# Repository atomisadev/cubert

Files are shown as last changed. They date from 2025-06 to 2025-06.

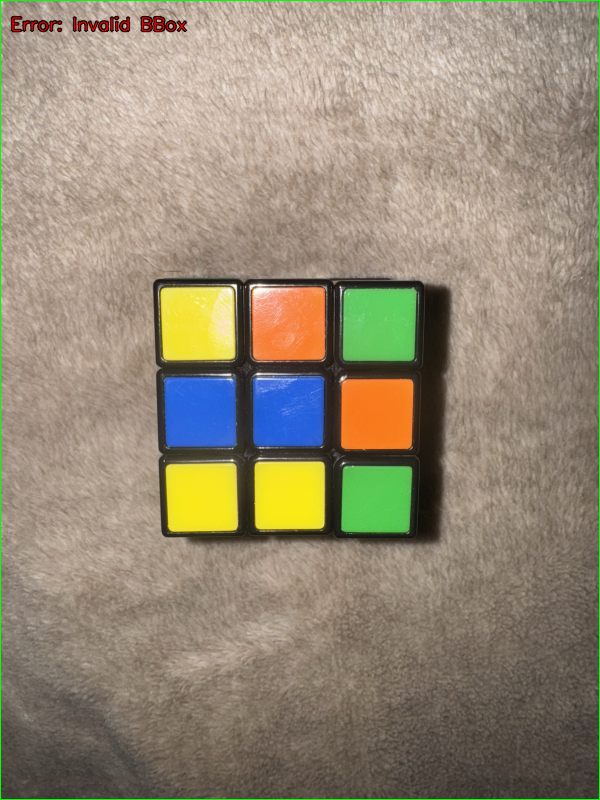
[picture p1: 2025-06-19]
apps/analyzer/debug_output/face-blue_debug.png

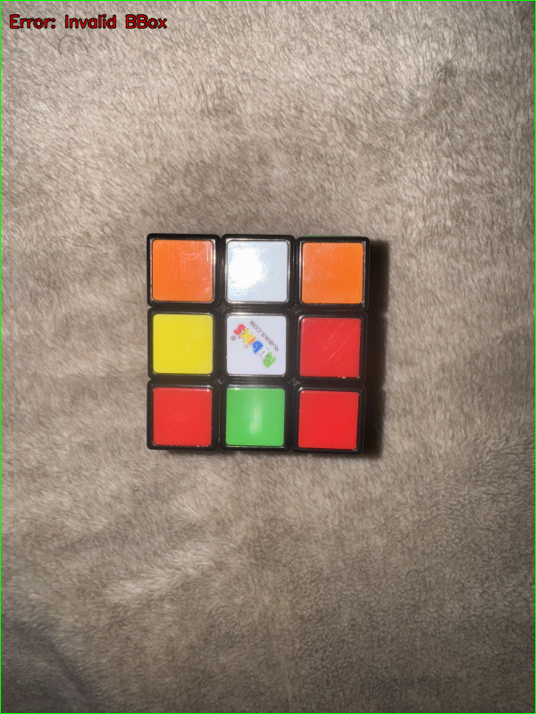
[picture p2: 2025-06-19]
apps/analyzer/debug_output/face-white_debug.png

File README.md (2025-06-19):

# Cubert

Cubert is a machine that automatically solves a 3x3x3 Rubik's Cube. It uses a Raspberry Pi and a phone's camera to scan the cube's scrambled state, calculates the solution using the Kociemba solving algorithm, and then runs the moves using a series of servo motors. 

We built this project to challenge ourselves and also dive deeper into electronics and mechanical design. I think that this project is an amazing learning experience that combines a lot of important aspects of engineering in the modern day, such as Python, CV, power and electronics, and also 3D printing. Overall, I believe we will have an amazing time building this project, whilst testing our ability to problem solve and also bonding together as friends.

> [!NOTE]  
> The CAD model can be found inside the root directory in the repository as STEP files.

## Project Images





## BOM
|Item Name |Item Link |Unit Price|Quantity|Vendor |Covered|Category |Total Price|
|---|---|---|---|---|---|---|---|
|MG996R Servo |https://www.aliexpress.us/item/3256808845498505.html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 |$22.07 |1 |Aliexpress| |Electronics|$22.07 |
|PCA9685 16-Channel I2C Servo Driver|https://www.aliexpress.us/item/3256808921151237.html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 |$9.57 |1 |Aliexpress| |Electronics|$9.57 |
|12V8A (96W) DC Adapter |https://www.amazon.com/TOBWOLF-100V-240V-Transformer-Switching-Converter/dp/B0B1DGBVKB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 |$13.49 |1 |Amazon | |Electronics|$13.49 |
|LTC3780 Buck Converter |https://www.aliexpress.us/item/3256807765142271.html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 |$15.93 |1 |Aliexpress| |Electronics|$15.93 |
|SSD1306 Displays |https://www.aliexpress.us/item/3256805315188857.html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 |$0.99 |1 |Aliexpress| |Electronics|$0.99 |
|Jumper Wires |https://www.aliexpress.us/item/3256805315188857.html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 |$0.99 |3 |Aliexpress| |Electronics|$2.97 |
|Raspberry Pi 4 Model B |https://www.aliexpress.us/item/3256806453128652.html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 |$74.02 |1 |Aliexpress| |Software |$74.02 |
|Micro SD Card |https://www.aliexpress.us/item/3256807418106088.html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 |$0.99 |2 |Aliexpress| |Software |$1.98 |
|PLA |https://www.amazon.com/Printer-Filament-SUNLU-Dimensional-Accuracy/dp/B07XG3RM58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 |$13.99 |1 |Amazon | | |$13.99 |
|FR-4 Perfboard |https://www.aliexpress.us/item/3256807592369547.html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 |$0.99 |2 |Amazon | |Electronics|$1.98 |
|GPIO Ribbon Cable |https://www.adafruit.com/product/1988?srsltid=AfmBOopw0o6-PRxXk69fa-PyLFZHPhA7xfmFhpCKWYBd3u95Ml1vz8VJ |$2.95 |2 |Adafruit  | |Electronics|$5.90 |
|AMS1117-3.3 LDO 3.3V |https://www.mouser.com/ProductDetail/Texas-Instruments/LM1117MPX-3.3-NOPB?qs=X1J7HmVL2ZHRbBIxXi4utg%3D%3D |$0.95 |1 |Mouser | |Electronics|$0.95 |
|Breadboard (prototyping |https://www.amazon.com/DEYUE-breadboard-Set-Prototype-Board/dp/B07LFD4LT6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 |$6.48 |1 |Amazon | |Electronics|$6.48 |
|40 pin male header |https://www.amazon.com/Hotop-Pack-Single-Header-Connector/dp/B06XR8CV8P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 |$7.59 |1 |Amazon | |Electronics|$7.59 |
|dupont wire kit |https://www.aliexpress.us/item/3256808956283599.html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 |$6.97 |1 |Aliexpress| |Electronics|$6.97 |
|18 awg gauge wire |https://www.amazon.com/Automotive-Flexible-Security-Stranded-Electrical/dp/B0CKR35SX5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 |$6.99 |1 |Amazon | |Electronics|$6.99 |
|22 awg gauge wire |https://www.aliexpress.us/item/3256808390015187.html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 |$3.64 |1 |Aliexpress| |Electronics|$3.64 |
|1000uf electrolytic capacitor |https://www.mouser.com/ProductDetail/Rubycon/35ZLR1000MEFC12.5X20?qs=iLKYxzqNS74Eu5GjfP8u0A%3D%3D |$2.01 |1 |Mouser | |Electronics|$2.01 |
|m3 standoff kit |https://www.amazon.com/Csdtylh-Male-Female-Standoff-Stainless-Assortment/dp/B06Y5TJXY1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|$14.98 |1 |Amazon | |Mechanical |$14.98 |
|GAN 356 M |https://www.aliexpress.us/item/3256808398845129.html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 |$9.41 |1 |Aliexpress| |Cube |$9.41 |

## Total Cost
The total cost of the project, when summing up everything in the BOM is **$221.91**. However, I can bear the cost of the Raspberry Pi 4 Model B as I have one of my own. So, the final cost comes out to be **$147.89**.

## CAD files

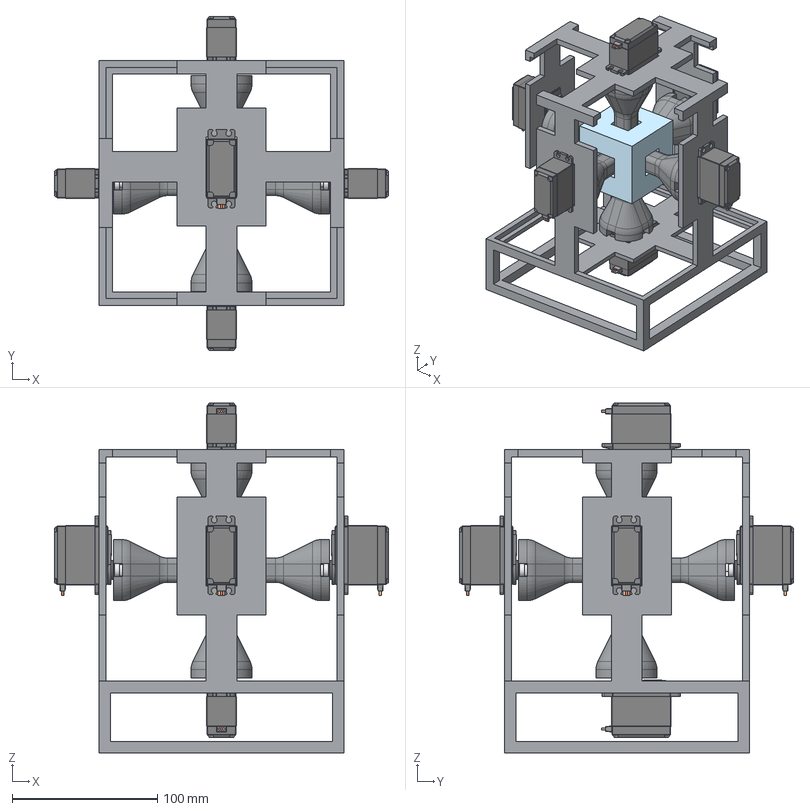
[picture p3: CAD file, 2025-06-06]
Main V0.step
230.0 x 230.0 x 240.8 mm
Servo MG996R arm01 x 6
Servo MG996R x 6
V0 Adapter x 6
Servo MG996R Shaft x 6
Frame V0
rubiks cube

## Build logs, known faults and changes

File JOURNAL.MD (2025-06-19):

---
title: "Cubert"
author: "Mohit Srinivasan and Alex Masin"
description: "A fully custom Rubik's cube solver!"
created_at: "2025-05-26"
---

### Total Time Spent
- Mohit: 10h
- Alex: 11.5h

# Day 1&2: Mohit
Hi everyone, this is where I'll be documenting the software aspect of the Cubert project. My name is Mohit and I'm excited to begin this project. The following content is the barebones software implementation for our project.

## Software Overview
The plan right now for the rubik's cube solver is that the user will upload images of all 6 faces of the cube to an app, and the app will convey this information to either a Raspberry Pi or an ESP32 which will algorithmically solve the rubik's cube. This idea is rooted in the basis that the center blocks of rubik's cubes do not change. To that end, we can ask the user to upload an image of the yellow side, the white side, the green side, etc. After the user uploads this image, we will send it up to AWS Rekognition which will run an image recognition model/CV that we can use to identify the images. I plan on converting this image data using like an AWS Lambda function to a text representation like using JSON or something, and then upload that back to the user. The user will then be uploading this text representation directly to the RPI which will compute the moves to solve the cube. Initially, I had a plan to keep all of the image recognition, etc. running on the RPI but realized how slow this actually is and decided to bring that part up to the cloud. We can also have a 3D Rubik's cube we display on the app for users that don't want to upload images, and instead they can just paint the cube with colors instead of actually taking images.

## Rough Excalidraw Diagram


## Code setup
I have the starter code setup in the repository. I am currently on vacation, hence I don't have access to my hardware. So, I have setup an ESP32 Simulation using Wokwi and PlatformIO. The code consists of a Turborepo monorepo management system which has an app called `mobile`. This `mobile` app inside Turborepo will contain all of the code for the mobile app. The current plan is to have the mobile app built using React Native and Expo, however I might change this if I run into some annoying issues and move to Flutter instead. I want to stay as far away from custom building apps for both Android and iOS and would love to just use a phone-agnostic library like Flutter or React Native.

### Time Spent: 1.5 hours

# Day 1&2: Alex

Hey all, this is where I'll be documenting my progress on the design/fabrication portion of the build. My name is Alex, and I am really excited to get started! 

Below is the rough proposal for the mechanical aspect of the build. This was the first step of the planning and is obviously very vague. But, here it is, to give you some context: 

## Design Process Overview

### Structure
Lightweight PLA 3D printed see-through web-design cage encompasses the rubik's cube, with a hole in the center of each face for where the servo motors will go.
There will be an armature piece on each face that directly connects from the servo output to the centerpiece of the rubik's cube face, either completely replacing the center piece or encompassing the center piece

### Unique Adapters
An adapter will be designed and fabricated for the servo output, as well as an adapter for the centerpiece on each rubik's cube face. Purdue ECE did it by creating new center pieces that mounted to the rubik’s cube and also could mount to the armature.

### Wire Routing
The cage will have sides to which all the wires will be fastened
### Potential issue(s)
The main issue I'm foreseeing with this design is figuring out the adapters and figuring out a way to make the rubik's cube easily removable from the cage.

## V0 Adapter 

The first step for me was to design a temporary adapter that would serve as the connection from the servos that spin each side to the actual face of the Rubik's Cube. I'm currently using the [Purdubiks machine](https://www.youtube.com/watch?v=sXxh6QuY2ew) as inspiration, with the idea being to create an adapter that directly interacts with the interior of the center dot. I'm using a random 3-D model of a speed cube for reference for now, as I don't actually own a Rubik's cube yet, but I'm really hoping that the kind person who modeled the cube modeled it true to life. Enough yap, this is what we're working with currently:



Bear in mind, this is just meant to be a proof of concept to me that my idea works. This will become much more refined once more details are finalized. but this is what we have for now. 

### Total Time Spent: 2 Hrs 

# Day 3: Mohit

Day 3 was the day where I started working on coding the vision aspect of the project. As I said earlier, I was initially planning on making it a mobile app using React Native or Flutter. I said that if React Native got annoying, I'd switch to Flutter. I changed my mind again. The final revision of the app will be.... **a Next.js app!**

The reason I made the switch is because a mobile app is overkill for the purpose of this project, and we just need the UI and the app to be barebones. As in the future we plan on turning this into a $350 project by possibly adding cameras (not confirmed). And, if we do decide to do that, a mobile app is quite pointless (boo overengineering 👎). 

## How vision works
So the vision code analyzes images of each face to find out its colors. First, an image of a single face is loaded, then its resized (to be consistent), and then it's converted from BGR to HSV (Hue, Saturation, Value) color space (this works quite better for color detection). I then apply a Gaussian blur to reduce any noise that might be present on the image. I then create a segmentation mask using predefined HSV thresholds (should be found inside `config.py`) and this isolates the background from the cube. There are other morphological operations that are at play that make the mask more clearer and better quality. So given that mask, the largest contour, is assumed to be the face of the cube, and is identified and approximated to a polygon. The area is then divided into a 3x3 grid and I map smaller ROIs (regions of interest) and define them within each of the 9 sticker areas. For each of the sampling ROI, I calculate the average HSV value. That avg HSV value tuple is compared against some other predefined HSV ranges (defined in the config) to determine the right color character (ex. `W` for white, `R` for red). Then the detected colors for each sticker are then put together into a 3x3 grid representing the face and then I repeat that same process to build a cube string (filled with the entire cube state). Throughout the entire thing I can run debug visualizations to make my life much easier.

## Why I moved away from AI?
At the beginning I started thinking of using AWS Rekognition for image recognition. However, I believe this is actual over-engineering and that a Raspberry Pi should be able to run moderate vision algos (like the one mentioned above) quite fast. Having everything locally would mean that the machine can run without a steady internet connection. 

## How can I improve this in the future?
I believe i can make the color detection more robust if instead of relying on predefined HSV thresholds, I can have some sort of automatic color calibration routine. Like the user can present each face's center sticker to the camera under their current lighting conditions & the system can learn the appropriate HSV ranges for each color. This is the closest I can get to actually using a machine learning model, but that's overkill. 

I can also probably improve the geometric analysis of the cube. Right now the system relies on finding the largest contour and then fitting a 3x3 grid to its bounding box. This can be less accurate if the cube is held at an angle which can lead to some kind of distortion. I guess in the future I can implement perspective correction based on the detected contour's shape (ex. by finding the 4 corner points of the face if it's sufficiently quadrilateral) before actually defining the sticker ROIs. There are some more advanced techniques, but I'm lowk just too dumb to figure them out.

The end solution to making everything work around 100% of the time would be to use a machine learning model like YOLO or SSD. This would remove all the tedious steps of contouring everything, making the grid, and the sampling all the ROIs individually. I think it would simplify the pipeline, but it's kinda overkill (idk my mind might change in the future after doing some electronics).

### Time spent: 3h
# Day 3

Day 3 was an easier day - I did a few minor things and that's about it. 

## Making my life easier 
 I created a reference cube (a cube with a hole on each face) to use for modeling purposes, as the imported model was not actually mated together. Here it is: 


## Assembling the Assembly  
I also started making the assembly of the cube - servo - adapter. 


With a few simple steps, I replicated this subassembly on each side of the reference cube. 


I also oriented each servo so that the cables would come out facing the front face (or could at least be easily routed towards the front face).

One thing Mohit and I have been worrying about is the adapter blocking the view of the cameras. Still, for now, we decided we won't be worrying about cameras and will require the user to upload pictures of each face of the cube before putting it in the machine. Perhaps in later stages we will incorporate cameras that will detect the color of each dot of each face. 
### Total Time Spent: 1.5 hr 

# Day 4: Mohit
Day 4 was an important day. It marks the first day I started designing, and thinking about the electronics for Cubert.

## Initial Plans
As mentioned in the previous days, we decided to ditch our effort towards having cameras on the robot, and instead the user just takes pictures of all the faces of the cube and then sends it to the robot. This is much more cost-efficient, because we believe we can keep the project under $150 if we take this approach to it. 

## Creating a BOM
This is the day I created a rough BOM of the items we'd need and then mapping it to listings I found on AliExpress (the cheapest ones I could find of course).



This is super rough and I'm only including the main components right now. We're still going to need filament, jumper cables, resistors, etc. Additionally, we have plans to turn our power distribution logic into a PCB so we're going to need money to print them out.

### Time Spent: 1.5 hr

# Day 4 

Today was the second big day, as I committed myself to designing the frame today. 

## Making the Frame 
I didn't really know where to start, so as before, I turned to [Purdue](https://www.youtube.com/watch?v=sXxh6QuY2ew). They obviously design at a much better level than me, but I figured I could still take inspiration from them. I also looked at [Aed Musa's Design](https://www.youtube.com/watch?v=m0bMMALYMYk), and decided to go for a middle of the road approach. This is what I came up with: 


Now, there are several issues with this design, so let's go through them. 
### 1. It's asymmetrical in a weird way 
Because of the way the servo is with the shaft being at one end of the overall block, I had to make the servo mounts off-center which makes everything look slightly weird, and also messes with the geometry. No big deal here other than being annoying. 
### 2. There's no real design for getting the cube in/out 
This is what I'm most worried about, but I figured for the prototype version I will just print the frame as is and wedge the Rubik's Cube in there. If my design concepts work, then I will redesign the frame to actually be user-friendly.
### 3. Bad visibility 
Mohit was complaining hard about this one, so I just got rid of the sides. All better now! 


### Final Touches 
I added a base, so the frame has something to stand on, and before I print it (more on that later) I'll be adding bolt/ziptie holes for the servo mounting. 

I'm going to admit, this frame isn't perfect, but it will (hopefully) do exactly what I need it to do, which is being a proof of concept.

This is what the full assembly currently looks like: 



### Time Spent : 2 Hrs
 
# Day 5: Mohit

This is the biggest day in our project so far. This is the day I designed out the entire electronics. 

## Schematic


## How this will work
The plan for the electronics is that we will have a 6V10A adapter that plugs into a wall. The Raspberry Pi requires 5V to run. So, we can use a DC-DC Buck Converter (I added the one we need to the BOM from Day 4) to step down the 6V to 5V and feed it into the RPI. When doing this in person, we'd need to make sure that the VOUT actually is stepping down 5.0V - 5.1V using a multimeter but that's a thought for another day. We then take 6V directly from the adapter and feed it to the servos on the PCA9685 servo board. The servo board's logic is powered by the 3.3V port from the RPI directly. Then each of the servos is connected to their respective PWM, V+, and GND. 

## Our main challenge
The main challenge right now is figuring out how we're going to place all the electronics inside the machine without it looking disgusting. We're both horrible at wire management and hiding everything, so we'll see how it all works out. We want to get all of these designs submitted & get our funding approved so we can start building it immediately!

This took way longer than I'd like to admit because to do this first, I had to learn Kicad 💀 

### Time Spent: 4h

# Day 5: Alex
Today is the day I finally got to printing parts of the project. 

## The Plan and Setup 
The first thing I wanted to verify was the dimensions of the adapter and make sure it actually interfaced properly with the cube. This was the scariest part, as I was finally going to have to test the trustworthiness of that random CAD model. Additionally, my current setup is a stock Prusa i3 MK3S+ with SUNLU Black PLA, and I use PrusaSlicer to slice all my files. 

## Printing the V0 adapter: First attempt
For this first one, I was foolish enough to think that it was going to work off the first attempt, so I printed it at 100% infill. It took roughly 3-4 hours to print, and was more or less a wasted time - 0-10% infill takes 1-1.5hrs. 
Here it is: 


## Printing the V0 adapter: Second attempt
The problem with the previous adapter is that the Rubik's end was too small in width, so for this one, I increased the width by 2mm to exactly match the size of the CAD model (it seems that the CAD model lines up with the GAN cube dimensions). I printed this one only at 5% infill, and it only took 1.5 hrs. As I probably should have expected, this one is about half a millimeter too big: 


## Getting smarter: Third attempt 
This time, instead of printing the entire adapter, I only printed the end bit. I ended up sizing down the width by 0.5 millimeters, and it fit perfectly! 



## V0 FINALIZED 
Alright, I finally printed the V0 adapter with the right sizing. I kept the infill low, _just in case_. Nothing to add, it fits perfectly, and is ready for further prototyping! 


That's a wrap for today, next day will involve more prototyping! 

### Time Spent: 1.5 Hours 

# Day 6: Mohit
I decided that it would be much better to add an SSD1306 to the schematics and electronics to make it more visual. It would be nice for the user to see like updates on the actual Cubert machine itself on if their app is connected, and if it's receiving the data and stuff (similar to a printer). So, I added an SSD1306.



One main issue is that the Raspberry Pi 3.3V output goes to the logic for the PCA9685 and we need another 3.3V port for the SSD1306. So a solution IRL would be to splice the wire, or we could have a 5V port and have a voltage regulator that steps down 5V to 3.3V for the SSD1306. Everything else is fine, but that's the only big issue.

### Time spent: 0.5h

# Day 6: Alex 

## Frame Redesign

I was told that the frame V0 is bad. Unfortunately, the haters are correct. So, I created Frame V1. 

To start, I realized that making the entire frame in a part studio is a bad idea, so I made it in an assembly instead. The biggest issue with V0 is that the entire frame was one piece, so I tried to make sure the frame was made of several individual parts. I retained the same type of design, using the same strips for each side: 



Next, I needed to figure out a way to bind all the sides together. I was stumped for some time, but then I realized that I could just use a 'cap' on the top and bottom that would keep everything secure.



I made the top cap a little bit shorter for visibility purposes. Next, I needed to make a stand to hold the machine. Looking at the stool in my room, I was inspired to make a stool: 



Anyway, this is the final V1 assembly. I think this one will actually work. 



Some notes:
* This version has accurate mounting holes
* I included all fasteners 
* electronics will be mounted on the bottom face of the machine, around the servo. 

### Time Spent: 3 Hours

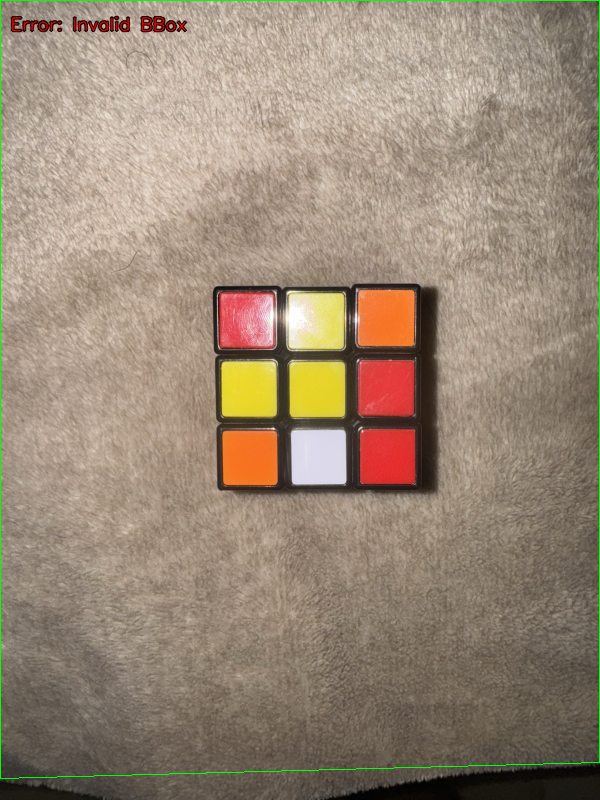
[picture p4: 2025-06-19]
apps/analyzer/debug_output/face-yellow_debug.png

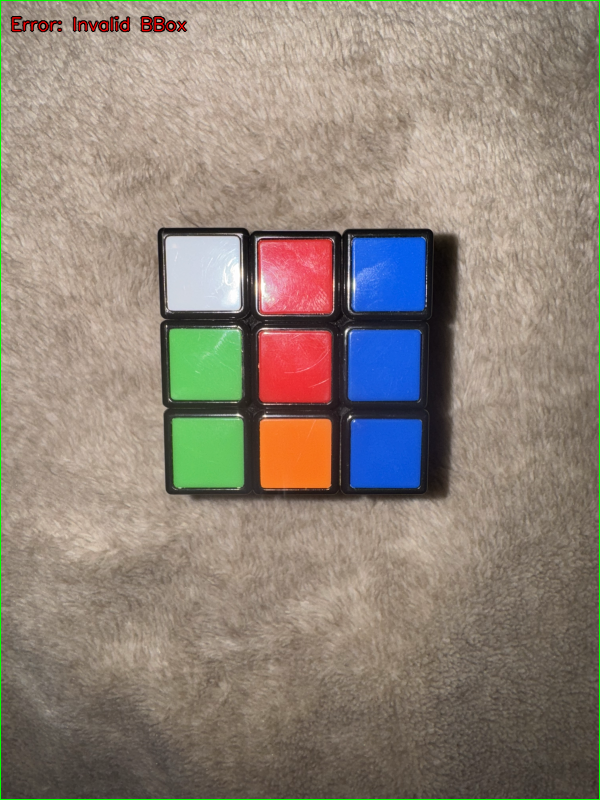
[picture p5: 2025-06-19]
apps/analyzer/debug_output/face-red_debug.png

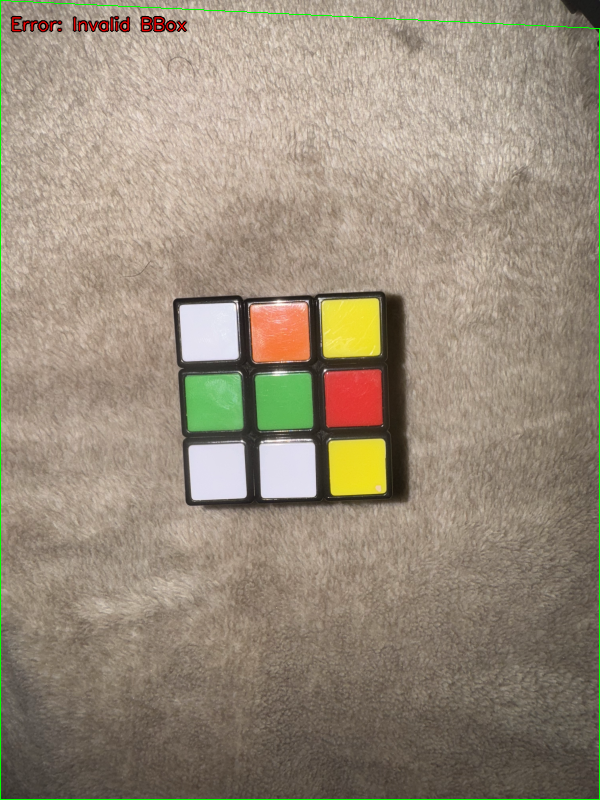
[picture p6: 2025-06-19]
apps/analyzer/debug_output/face-green_debug.png

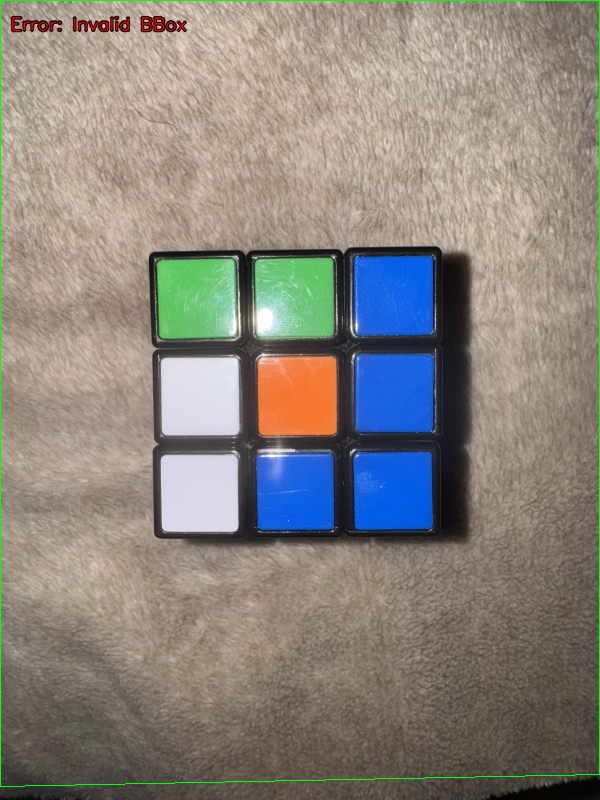
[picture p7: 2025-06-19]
apps/analyzer/debug_output/face-orange_debug.png

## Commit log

2025-05-27 device unsupported for desktops
2025-06-06 Project BOM
    [BOM.csv]
2025-06-06 CAD file
    [Main V0.step]
